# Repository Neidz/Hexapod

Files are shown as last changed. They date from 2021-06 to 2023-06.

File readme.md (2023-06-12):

<b>Update: Well, this code is really bad but if you still want to use it then go ahead, it will work... kinda. No idea what past me was thinking writing it.</b>

<p>This is 3D printed hexapod that I build, it runs on Raspberry Pi, uses 18 servo motors for movement and is controlled from app on the phone. I started this project about year ago and didn't visit it for quite some time but I decided that it's still worth sharing because someone might want find models or code (communication between Raspberry Pi and servo control board was kinda tricky for me) useful.</p>

<h4>Here are some pictures:</h4>
<a>https://imgur.com/a/LP6Iy2R?nc=1</a>

<h4>And here are some videos</h4>
<a>https://www.youtube.com/watch?v=-9L5q-5OcWs</a> </br>
<a>https://www.youtube.com/watch?v=_HX3u8fKZZM</a>

<h4>Main goals of this project were:</h4>
<ul>
<li>building hexapod that is running on Raspberry Pi (there are a lot of them running on arduinos but I wanted to try building one on RPi and that project was my way of learning python)</li>
<li>-creating really affordable robot (most of the things used in my robot are really cheap, even 18 servo motors shouldn't be something out of reach for hobbyist</li>
</ul>

<h1>3D printed parts</h1>

<h4>If you want to print that hexapod you will have to print:</h4>
<ul>
<li>Base in 3 parts (Split_base_1.stl, Split_base_2.stl, Split_base_3.stl) or if you have large 3d printer you can connect parts in any program that allows stl manipulations and print is as one</li>
<li>Cover in 2 parts (Split_cover_1.stl, Split_cover_2.stl), the same things as with base here, if you are able then you can print it as one after connecting it in any program</li>
<li>First_part_of_the_leg.stl x3</li>
<li>First_part_of_the_leg.stl x3 after mirroring</li>
<li>Second_part_of_the_leg.stl x3</li>
<li>Second_part_of_the_leg.stl x3 after mirroring</li>
<li>Third_part_of_the_leg.stl x3</li>
<li>Third_part_of_the_leg.stl x3 after mirroring</li>
  </ul><br>
<p>You have to print all leg parts 3 times and then print them 3 more times after mirroring
I printed all the parts with PLA, 0,1mm layer height worked best for overhangs but you can probably go with 0,2mm, all parts other than cover sadly need some supports</p>

<h1>Software</h1>

<p>I wrote the code in python and it's meant to be run on Raspberry Pi (i used 3b+), I'm uploading this project some time after I actually created it so the way robot is getting all the commands is quite weird but basically: raspberry pi runs 2 programs, one is called Hexapod_server.py and it starts requestHandler which constantly writes all requests it's getting into Requests.txt, after that Hexapod_final.py grabs them from the file and executes functions connected to those requests
<br>
Not the best solution but at the time this was the best things that I came up with while being absolute python noob. To send requests I also created app with Mit app inventorr (not the most elegant thing but once again it was all I could make at the time)</p>

<h4>Setup</h4>
<ul>
<li>in Hexapod_server.py you have to change "Change it to your ip" in line 30 to... well, your ip</li>
<li>in app you have to also pass your ip and click "Set"</li>
</ul>
<h1>Hardware</h1>
<ul>
<li>raspberry pi of your choice (I used 3b+ here)</li>
<li>buck converter that can handle at least 10A at 6,5V for all 18 servos (I used 300W 20A buck converter from aliexpress and it worked fine)</li>
<li>suitable powerbank or next buck converter to power up raspberry pi</li>
<li>MG995 55g servo x18</li>
<li>25T M3 Metal RC Servo Arm Horn x18 (I used this one aliexpress.com/item/4000957433782.html?spm=a2g0s.9042311.0.0.adbd5c0fBZJcos)</li>
<li>at least 18 channel servo control board that is able to handle previously mentioned power (I used this 32 channel board aliexpress.com/item/32272674301.html?spm=a2g0s.9042311.0.0.27425c0f2JeqpC)</li>
<li>battery, preferably 3S, at least 2000mAhm and if you want to also power up raspberry pi from the same battery then I would go for 3000mAh+ (with 2000mAh 3S battery i was able to use hexapod for about 20 minutes while powering raspberry pi from separate powerbank)</li>
<li>cables and connectors of your choice, I wouldn't use jumper wires for main power to servo control board because they are very thin but if you are feeling spicy and like the smell of burning insulation then go ahead </li>
<li>a lot of m3 bolts and preferably m3 locknuts (vibrations cause normal nuts to slowly unscrew)</li>
</ul>

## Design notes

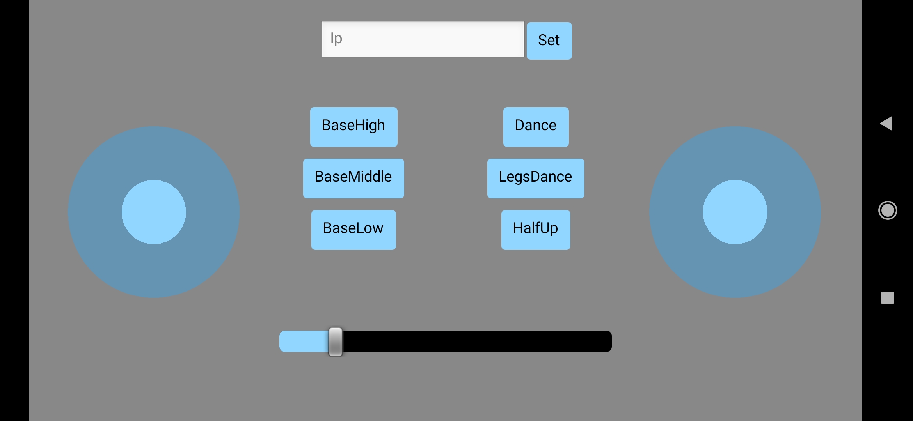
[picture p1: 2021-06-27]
Media/App for hexapod control.jpg

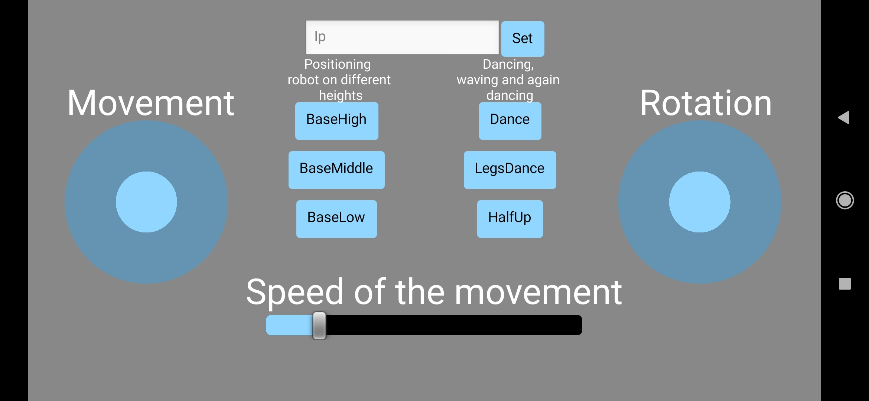
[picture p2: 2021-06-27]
Media/How app works.png

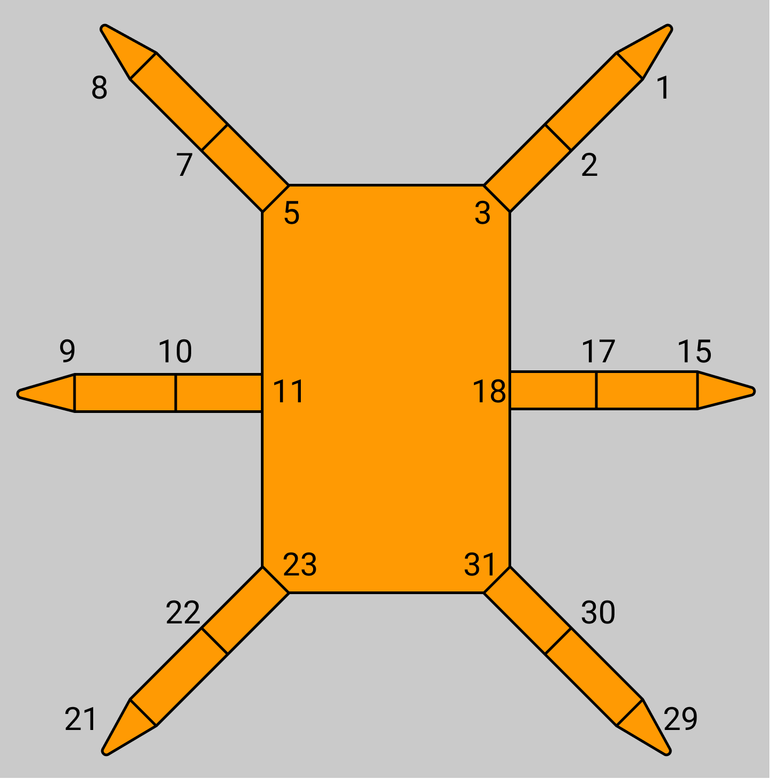
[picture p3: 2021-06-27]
Media/Servo connection.png

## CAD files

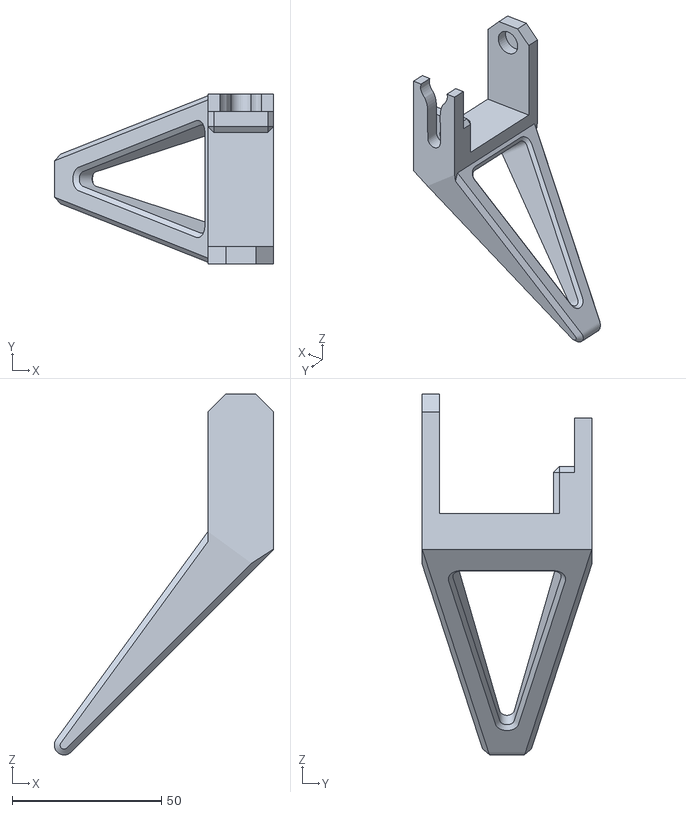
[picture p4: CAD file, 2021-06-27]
Parts stls/Third_part_of_the_leg.stl
73.4 x 57.0 x 120.8

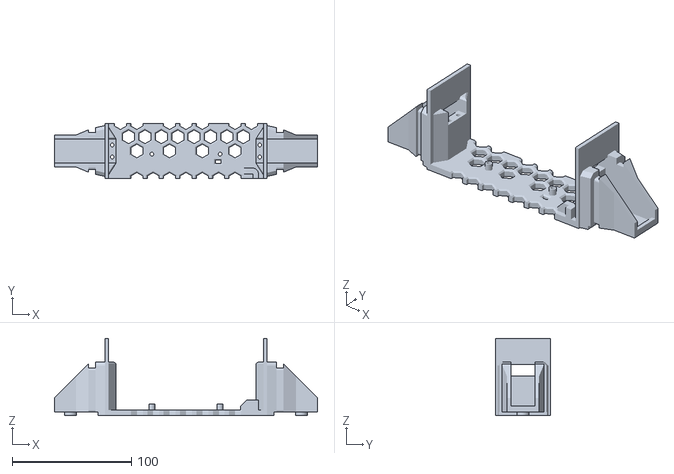
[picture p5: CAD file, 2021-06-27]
Parts stls/Split_base_3.stl
220.8 x 46.0 x 65.0

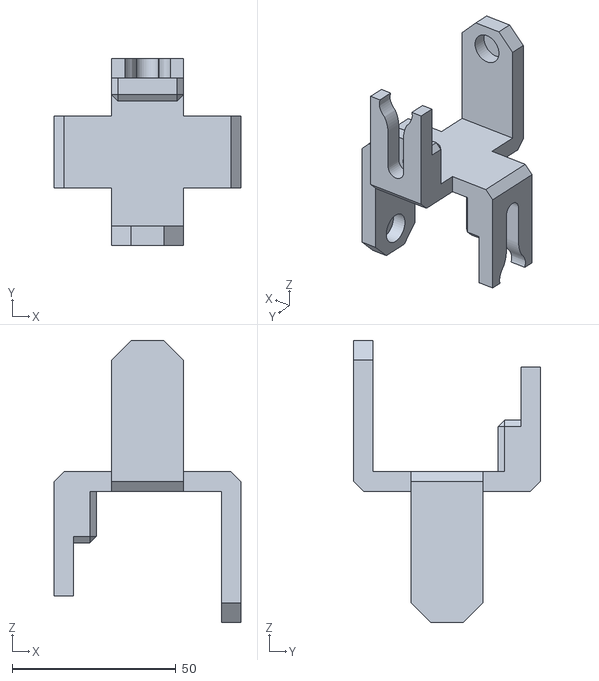
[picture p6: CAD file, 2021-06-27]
Parts stls/First_part_of_the_leg.stl
57.0 x 57.0 x 86.0

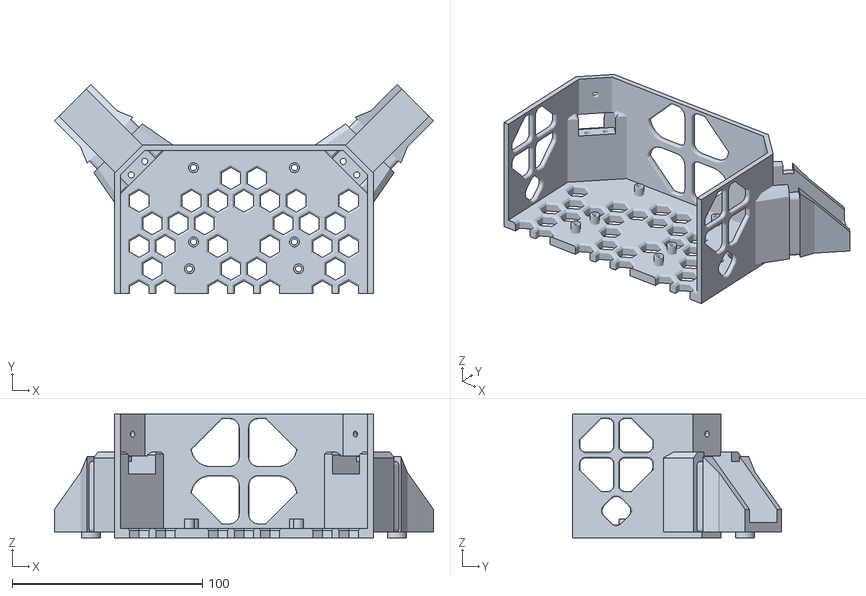
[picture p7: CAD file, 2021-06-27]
Parts stls/Split_base_1.stl
199.0 x 109.6 x 65.0

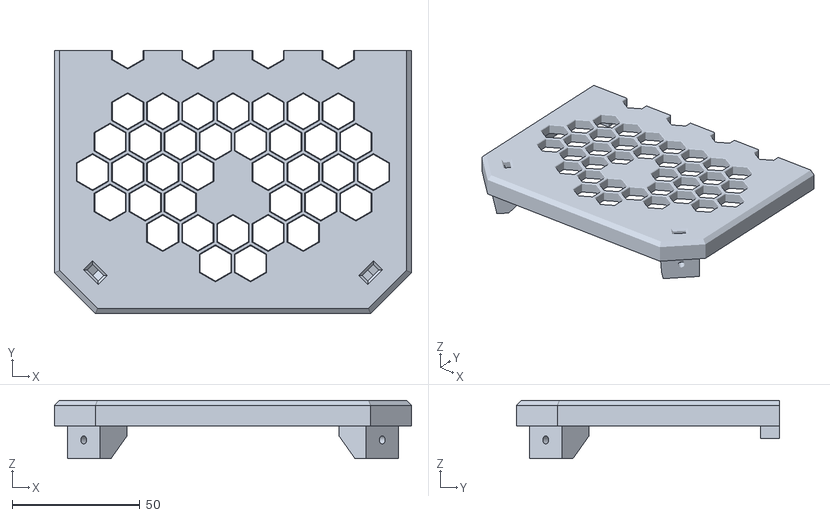
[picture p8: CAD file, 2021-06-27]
Parts stls/Split_cover_2.stl
139.8 x 103.0 x 22.9

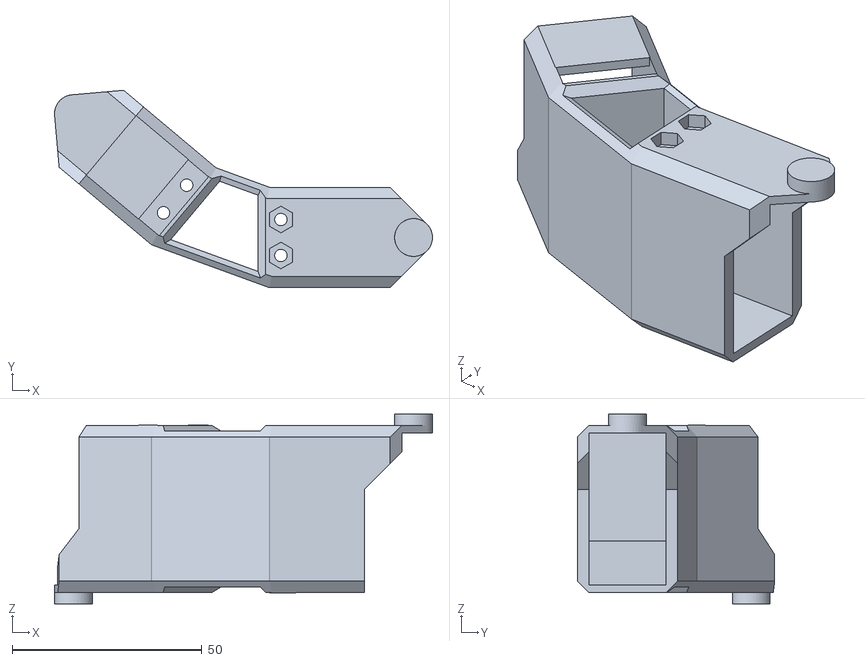
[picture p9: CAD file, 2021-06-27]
Parts stls/Second_part_of_the_leg.stl
99.7 x 52.1 x 50.0

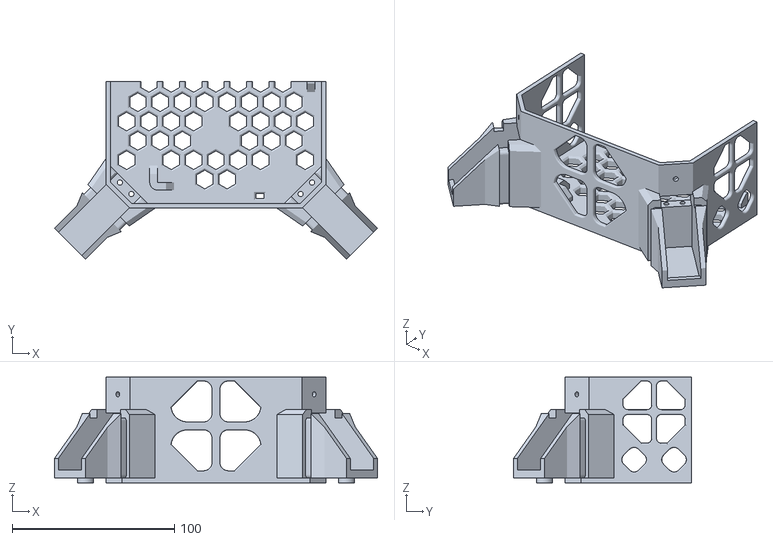
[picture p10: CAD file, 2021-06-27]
Parts stls/Split_base_2.stl
199.0 x 109.6 x 65.0

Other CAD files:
Parts stls/Split_cover_1.stl

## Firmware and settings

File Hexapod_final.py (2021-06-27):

import serial
import time

if __name__ == '__main__':
    ser = serial.Serial('/dev/ttyACM0', baudrate=115200,
                        parity=serial.PARITY_NONE,
                        stopbits=serial.STOPBITS_ONE,
                        bytesize=serial.EIGHTBITS
                        )

fastsleep = 0.5
base = 1500
p2 = p3 = p5 = p6 = p8 = p9 = p11 = p12 = p14 = p15 = p17 = p18 = 1500
p1 = p4 = p7 = 1650
p10 = p16 = p13 = 1350
change = 350
change2 = 170
change3 = change2*2
change4 = 350
change5 = 300
speed = 70
sleep = speed / 1000 + 0.1
slow = 1000
delay = 0
t = 5
hight = "normal"
Request = "base\n"
Request2 = "boop"

def Prepare():
    global base, speed, slow, delay, p1, p2, p3, p4, p5, p6, p7, p8, p9, p10, p11, p12, p13, p14, p15, p16, p17, p18
    base = int(base)
    speed = int(speed)
    slow = int(slow)
    p1, p2, p3, p4, p5, p6, p7, p8, p9, p10, p11, p12, p13, p14, p15, p16, p17, p18 = int(p1), int(p2), int(p3), int(
        p4), int(p5), int(p6), int(p7), int(p8), int(p9), int(p10), int(p11), int(p12), int(p13), int(p14), int(
        p15), int(p16), int(p17), int(p18)


def Reset():
    global base, speed, slow, delay, p1, p2, p3, p4, p5, p6, p7, p8, p9, p10, p11, p12, p13, p14, p15, p16, p17, p18
    base = 1500
    speed = 500
    slow = 1000
    p1 = p2 = p3 = p4 = p5 = p6 = p7 = p8 = p9 = p10 = p11 = p12 = p13 = p14 = p15 = p16 = p17 = p18 = 1500


def BasePosition():
    global base, speed, slow, delay, p1, p2, p3, p4, p5, p6, p7, p8, p9, p10, p11, p12, p13, p14, p15, p16, p17, p18
    if hight == "normal":
        Prepare()
        p2 = p3 = p5 = p6 = p8 = p9 = p11 = p12 = p14 = p15 = p17 = p18 = 1500
        p1 = p4 = p7 = 1650
        p10 = p16 = p13 = 1350
        basep = f"#1P{p10}#2P{p11}#3P{p12}#5P{p3}#7P{p2}#8P{p1}#9P{p4}#10P{p5}#11P{p6}#15P{p13}#17P{p14}#18P{p15}#21P{p7}#22P{p8}#23P{p9}#29P{p16}#30P{p17}#31P{p18}T{speed}D{delay}\r\n".encode()
        ser.write(basep)
    if hight == "low":
        Prepare()
        p3 = p6 = p9 = p12 = p15 = p18 = 1500
        p2 = p5 = p8 = 1200
        p1 = p4 = p7 = 1950
        p11 = p14 = p17 = 1800
        p10 = p16 = p13 = 1050
        basep = f"#1P{p10}#2P{p11}#3P{p12}#5P{p3}#7P{p2}#8P{p1}#9P{p4}#10P{p5}#11P{p6}#15P{p13}#17P{p14}#18P{p15}#21P{p7}#22P{p8}#23P{p9}#29P{p16}#30P{p17}#31P{p18}T{speed}D{delay}\r\n".encode()
        ser.write(basep)
    if hight == "high":
        Prepare()
        p3 = p6 = p9 = p12 = p15 = p18 = 1500
        p2 = p5 = p8 = 1800
        p1 = p4 = p7 = 1350
        p11 = p14 = p17 = 1200
        p10 = p16 = p13 = 1650
        basep = f"#1P{p10}#2P{p11}#3P{p12}#5P{p3}#7P{p2}#8P{p1}#9P{p4}#10P{p5}#11P{p6}#15P{p13}#17P{p14}#18P{p15}#21P{p7}#22P{p8}#23P{p9}#29P{p16}#30P{p17}#31P{p18}T{speed}D{delay}\r\n".encode()
        ser.write(basep)





def Movement():
    movement = f"#1P{p10}#2P{p11}#3P{p12}#5P{p3}#7P{p2}#8P{p1}#9P{p4}#10P{p5}#11P{p6}#15P{p13}#17P{p14}#18P{p15}#21P{p7}#22P{p8}#23P{p9}#29P{p16}#30P{p17}#31P{p18}T{speed}D{delay}\r\n".encode()
    ser.write(movement)


def HalfUp():
    global base, speed, slow, delay, p1, p2, p3, p4, p5, p6, p7, p8, p9, p10, p11, p12, p13, p14, p15, p16, p17, p18
    BasePosition()
def HalfUp2():
    global base, speed, slow, delay, p1, p2, p3, p4, p5, p6, p7, p8, p9, p10, p11, p12, p13, p14, p15, p16, p17, p18
    time.sleep(sleep)
    Prepare()
    p1, p2, p7, p8 = p1 + change, p2 - change, p7 + change, p8 - change
    p13, p14 = p13 - change, p14 + change
    Movement()
    time.sleep(sleep)
    BasePosition()
    time.sleep(sleep)
    Prepare()
    p4, p5 = p4 + change, p5 - change
    p10, p11, p16, p17 = p10 - change, p11 + change, p16 - change, p17 + change
    Movement()
    time.sleep(sleep)
    BasePosition()
    LineCheck()

def Dance():
    global base, speed, slow, delay, p1, p2, p3, p4, p5, p6, p7, p8, p9, p10, p11, p12, p13, p14, p15, p16, p17, p18
    BasePosition()
def Dance2():
    global base, speed, slow, delay, p1, p2, p3, p4, p5, p6, p7, p8, p9, p10, p11, p12, p13, p14, p15, p16, p17, p18
    time.sleep(sleep)
    Prepare()
    p1, p2, p3, p16, p17, p18 = p1 + change, p2 - change, p3 + change4, p16 - change, p17 + change, p18 + change4
    Movement()
    time.sleep(sleep)
    Prepare()
    p1, p2, p16, p17 = p1 - change, p2 + change, p16 + change, p17 - change
    Movement()
    time.sleep(sleep)
    Prepare()
    p1, p2, p3, p16, p17, p18 = p1 + change, p2 - change, p3 - change4, p16 - change, p17 + change, p18 - change4
    Movement()
    time.sleep(sleep)
    Prepare()
    p1, p2, p16, p17 = p1 - change, p2 + change, p16 + change, p17 - change
    Movement()
    time.sleep(sleep)
    Prepare()
    p10, p11, p12, p7, p8, p9 = p10 - change, p11 + change, p12 - change4, p7 + change, p8 - change, p9 - change4
    Movement()
    time.sleep(sleep)
    Prepare()
    p10, p11, p7, p8, = p10 + change, p11 - change, p7 - change, p8 + change
    Movement()
    time.sleep(sleep)
    Prepare()
    p10, p11, p12, p7, p8, p9 = p10 - change, p11 + change, p12 + change4, p7 + change, p8 - change, p9 + change4
    Movement()
    time.sleep(sleep)
    Prepare()
    p10, p11, p7, p8, = p10 + change, p11 - change, p7 - change, p8 + change
    Movement()
    time.sleep(sleep)
    Prepare()
    LineCheck()


def Forward():
    global base, speed, slow, delay, p1, p2, p3, p4, p5, p6, p7, p8, p9, p10, p11, p12, p13, p14, p15, p16, p17, p18
    BasePosition()
    time.sleep(sleep)
    Prepare()
    p7, p8, p9 = p7 + change, p8 - change, p9 - change4
    Movement()
    time.sleep(sleep)
    Prepare()
    p7, p8 = p7 - change, p8 + change
    Movement()
    time.sleep(sleep)
    Prepare()
    p16, p17, p18 = p16 - change, p17 + change, p18 + change4
    Movement()
    time.sleep(sleep)
    Prepare()
    p16, p17 = p16 + change, p17 - change
    Movement()
    time.sleep(sleep)
    Prepare()
    p1, p2, p7, p8, p13, p14, p15 = p1 + change, p2 - change, p7 + change, p8 - change, p13 - change, p14 + change, p15 + change2
    p6, p12, p18 = p6 + change2, p12 - change4, p18 - change4
    Movement()
    time.sleep(sleep)
def Forward2():
    global base, speed, slow, delay, p1, p2, p3, p4, p5, p6, p7, p8, p9, p10, p11, p12, p13, p14, p15, p16, p17, p18
    Prepare()
    p1, p2, p7, p8, p13, p14 = p1 - change, p2 + change, p7 - change, p8 + change, p13 + change, p14 - change
    Movement()
    time.sleep(sleep)
    Prepare()
    p3, p9, p15 = p3 + change4, p9 + change4, p15 - change3
    p6, p12, p18 = p6 - change3, p12 + change4, p18 + change4
    p4, p5, p10, p11, p16, p17 = p4 + change, p5 - change, p10 - change, p11 + change, p16 - change, p17 + change
    Movement()
    time.sleep(sleep)
    Prepare()
    p4, p5, p10, p11, p16, p17 = p4 - change, p5 + change, p10 + change, p11 - change, p16 + change, p17 - change
    Movement()
    time.sleep(sleep)
    Prepare()
    p6, p12, p18 = p6 + change3, p12 - change4, p18 - change4
    p3, p9, p15 = p3 - change4, p9 - change4, p15 + change3
    p1, p2, p7, p8, p13, p14 = p1 + change, p2 - change, p7 + change, p8 - change, p13 - change, p14 + change
    Movement()
    time.sleep(sleep)
    LineCheck()

def Back():
    global base, speed, slow, delay, p1, p2, p3, p4, p5, p6, p7, p8, p9, p10, p11, p12, p13, p14, p15, p16, p17, p18
    BasePosition()
    time.sleep(sleep)
    Prepare()
    p1, p2, p3 = p1 + change, p2 - change, p3 + change4
    Movement()
    time.sleep(sleep)
    Prepare()
    p1, p2 = p1 - change, p2 + change
    Movement()
    time.sleep(sleep)
    Prepare()
    p10, p11, p12 = p10 - change, p11 + change, p12 - change4
    Movement()
    time.sleep(sleep)
    Prepare()
    p10, p11 = p10 + change, p11 - change
    Movement()
    time.sleep(sleep)
    Prepare()
    p1, p2, p7, p8, p13, p14, p15 = p1 + change, p2 - change, p7 + change, p8 - change, p13 - change, p14 + change, p15 - change2
    p6, p12, p18 = p6 - change2, p12 + change4, p18 + change4
    Movement()
    time.sleep(sleep)
def Back2():
    global base, speed, slow, delay, p1, p2, p3, p4, p5, p6, p7, p8, p9, p10, p11, p12, p13, p14, p15, p16, p17, p18
    Prepare()
    p1, p2, p7, p8, p13, p14 = p1 - change, p2 + change, p7 - change, p8 + change, p13 + change, p14 - change
    Movement()
    time.sleep(sleep)
    Prepare()
    p3, p9, p15 = p3 - change4, p9 - change4, p15 + change3
    p6, p12, p18 = p6 + change3, p12 - change4, p18 - change4
    p4, p5, p10, p11, p16, p17 = p4 + change, p5 - change, p10 - change, p11 + change, p16 - change, p17 + change
    Movement()
    time.sleep(sleep)
    Prepare()
    p4, p5, p10, p11, p16, p17 = p4 - change, p5 + change, p10 + change, p11 - change, p16 + change, p17 - change
    Movement()
    time.sleep(sleep)
    Prepare()
    p6, p12, p18 = p6 - change3, p12 + change4, p18 + change4
    p3, p9, p15 = p3 + change4, p9 + change4, p15 - change3
    p1, p2, p7, p8, p13, p14 = p1 + change, p2 - change, p7 + change, p8 - change, p13 - change, p14 + change
    Movement()
    time.sleep(sleep)
    LineCheck()

def TurnLeft():
    global base, speed, slow, delay, p1, p2, p3, p4, p5, p6, p7, p8, p9, p10, p11, p12, p13, p14, p15, p16, p17, p18
    BasePosition()
    time.sleep(sleep)
    Prepare()
    p1, p2, p7, p8, p13, p14 = p1 + change, p2 - change, p7 + change, p8 - change, p13 - change, p14 + change
    p3, p15 = p3 + change4, p15 + change2
    Movement()
    time.sleep(sleep)
    Prepare()
    p1, p2, p7, p8, p13, p14 = p1 - change, p2 + change, p7 - change, p8 + change, p13 + change, p14 - change
    Movement()
    time.sleep(sleep)
    Prepare()
    p3, p9, p15 = p3 - change4, p9 - change4, p15 - change3
    p4, p5, p10, p11, p16, p17 = p4 + change, p5 - change, p10 - change, p11 + change, p16 - change, p17 + change
    p6, p18 = p6 + change2, p18 + change4
    Movement()
    time.sleep(sleep)
def TurnLeft2():
    global base, speed, slow, delay, p1, p2, p3, p4, p5, p6, p7, p8, p9, p10, p11, p12, p13, p14, p15, p16, p17, p18
    Prepare()
    p4, p5, p10, p11, p16, p17 = p4 - change, p5 + change, p10 + change, p11 - change, p16 + change, p17 - change
    Movement()
    time.sleep(sleep)
    Prepare()
    p3, p9, p15 = p3 + change4, p9 + change4, p15 + change4
    p6, p12, p18 = p6 - change4, p12 - change4, p18 - change4
    p1, p2, p7, p8, p13, p14 = p1 + change, p2 - change, p7 + change, p8 - change, p13 - change, p14 + change
    Movement()
    time.sleep(sleep)
    Prepare()
    p1, p2, p7, p8, p13, p14 = p1 - change, p2 + change, p7 - change, p8 + change, p13 + change, p14 - change
    Movement()
    time.sleep(sleep)
    Prepare()
    p3, p9, p15 = p3 - change4, p9 - change4, p15 - change4
    p6, p12, p18 = p6 + change3, p12 + change4, p18 + change4
    p4, p5, p10, p11, p16, p17 = p4 + change, p5 - change, p10 - change, p11 + change, p16 - change, p17 + change
    Movement()
    time.sleep(sleep)
    LineCheck()


def TurnRight():
    global base, speed, slow, delay, p1, p2, p3, p4, p5, p6, p7, p8, p9, p10, p11, p12, p13, p14, p15, p16, p17, p18
    BasePosition()
    time.sleep(sleep)
    Prepare()
    p10, p11, p16, p17, p4, p5 = p10 - change, p11 + change, p16 - change, p17 + change, p4 + change, p5 - change
    p12, p6 = p12 - change4, p6 - change2
    Movement()
    time.sleep(sleep)
    Prepare()
    p10, p11, p16, p17, p4, p5 = p10 + change, p11 - change, p16 + change, p17 - change, p4 - change, p5 + change
    Movement()
    time.sleep(sleep)
    Prepare()
    p12, p18, p6 = p12 + change4, p18 + change4, p6 + change3
    p13, p14, p1, p2, p7, p8 = p13 - change, p14 + change, p1 + change, p2 - change, p7 + change, p8 - change
    p15, p9 = p15 - change2, p9 - change4
    Movement()
    time.sleep(sleep)
def TurnRight2():
    global base, speed, slow, delay, p1, p2, p3, p4, p5, p6, p7, p8, p9, p10, p11, p12, p13, p14, p15, p16, p17, p18
    Prepare()
    p13, p14, p1, p2, p7, p8 = p13 + change, p14 - change, p1 - change, p2 + change, p7 - change, p8 + change
    Movement()
    time.sleep(sleep)
    Prepare()
    p12, p18, p6 = p12 - change4, p18 - change4, p6 - change4
    p15, p3, p9 = p15 + change4, p3 + change4, p9 + change4
    p10, p11, p16, p17, p4, p5 = p10 - change, p11 + change, p16 - change, p17 + change, p4 + change, p5 - change
    Movement()
    time.sleep(sleep)
    Prepare()
    p10, p11, p16, p17, p4, p5 = p10 + change, p11 - change, p16 + change, p17 - change, p4 - change, p5 + change
    Movement()
    time.sleep(sleep)
    Prepare()
    p12, p18, p6 = p12 + change4, p18 + change4, p6 + change4
    p15, p3, p9 = p15 - change3, p3 - change4, p9 - change4
    p13, p14, p1, p2, p7, p8 = p13 - change, p14 + change, p1 + change, p2 - change, p7 + change, p8 - change
    Movement()
    time.sleep(sleep)
    LineCheck()

def FrontLegsDance():
    global base, speed, slow, delay, p1, p2, p3, p4, p5, p6, p7, p8, p9, p10, p11, p12, p13, p14, p15, p16, p17, p18
    BasePosition()
    time.sleep(sleep)
    Prepare()
    p4, p5, p6, p13, p14, p15 = p4 + change, p5 - change, p6 - change2, p13 - change, p14 + change, p15 + change2
    Movement()
    time.sleep(sleep)
    Prepare()
    p4, p5, p13, p14 = p4 - change, p5 + change, p13 + change, p14 - change
    Movement()
    time.sleep(sleep)
    Prepare()
    p8, p7, p17, p16 = p8 - change5, p7 + change5, p17 + change5, p16 - change5
    Movement()
    time.sleep(sleep)
    Prepare()
    p1, p2, p3, p10, p11, p12 = p1 - change*2.5, p2 - change*2.5, p3 - change4, p10 + change*2, p11 + change*2, p12 - change4
    Movement()
    time.sleep(sleep)
def FrontLegsDance2():
    global base, speed, slow, delay, p1, p2, p3, p4, p5, p6, p7, p8, p9, p10, p11, p12, p13, p14, p15, p16, p17, p18
    Prepare()
    p3, p12 = p3 + change4*1.5, p12 + change4*1.5
    Movement()
    time.sleep(sleep*3)
    Prepare()
    p3, p12 = p3 - change4*1.5, p12 - change4*1.5
    Movement()
    time.sleep(sleep*3)
    LineCheck()

def GoLeft():
    global base, speed, slow, delay, p1, p2, p3, p4, p5, p6, p7, p8, p9, p10, p11, p12, p13, p14, p15, p16, p17, p18
    BasePosition()
    time.sleep(sleep)
    Prepare()
    p13, p14 = p13 - change, p14 + change
    Movement()
    time.sleep(sleep)
    Prepare()
    p14 = p14 - change
    Movement()
    time.sleep(sleep)
    Prepare()
    p3, p9, p13 = p3 - change4, p9 + change4, p13 + change
    p4, p5, p10, p11, p12, p16, p17, p18 = p4 + change, p5 - change, p10 - change, p11 + change, p12 + change4, p16 - change, p17 + change, p18 - change4
    Movement()
    time.sleep(sleep)
    Prepare()
    p4, p5, p10, p11, p16, p17 = p4 - change, p5 + change, p10 + change, p11 - change, p16 + change, p17 - change
    Movement()
    time.sleep(sleep)
def GoLeft2():
    global base, speed, slow, delay, p1, p2, p3, p4, p5, p6, p7, p8, p9, p10, p11, p12, p13, p14, p15, p16, p17, p18
    Prepare()
    p4, p12, p18 = p4 + change, p12 - change4, p18 + change4
    p1, p2, p3, p7, p8, p9, p13, p14 = p1 + change, p2 - change, p3 + change4, p7 + change, p8 - change, p9 - change4, p13 - change, p14 + change
    Movement()
    time.sleep(sleep)
    Prepare()
    p1, p2, p7, p8, p14 = p1 - change, p2 + change, p7 - change, p8 + change, p14 - change
    Movement()
    time.sleep(sleep)
    Prepare()
    p3, p9, p13 = p3 - change4, p9 + change4, p13 + change
    p4, p5, p10, p11, p12, p16, p17, p18 = p4 - change, p5 - change, p10 - change, p11 + change, p12 + change4, p16 - change, p17 + change, p18 - change4
    Movement()
    time.sleep(sleep)
    Prepare()
    p5, p10, p11, p16, p17 = p5 + change, p10 + change, p11 - change, p16 + change, p17 - change
    Movement()
    time.sleep(sleep)
    LineCheck()

def GoRight():
    global base, speed, slow, delay, p1, p2, p3, p4, p5, p6, p7, p8, p9, p10, p11, p12, p13, p14, p15, p16, p17, p18
    BasePosition()
    time.sleep(sleep)
    Prepare()
    p4, p5 = p4 + change, p5 - change
    Movement()
    time.sleep(sleep)
    Prepare()
    p5 = p5 + change
    Movement()
    time.sleep(sleep)
    Prepare()
    p12, p18, p4 = p12 + change4, p18 - change4, p4 - change
    p13, p14, p1, p2, p3, p7, p8, p9 = p13 - change, p14 + change, p1 + change, p2 - change, p3 - change4, p7 + change, p8 - change, p9 + change4
    Movement()
    time.sleep(sleep)
    Prepare()
    p13, p14, p1, p2, p7, p8 = p13 + change, p14 - change, p1 - change, p2 + change, p7 - change, p8 + change
    Movement()
    time.sleep(sleep)
def GoRight2():
    global base, speed, slow, delay, p1, p2, p3, p4, p5, p6, p7, p8, p9, p10, p11, p12, p13, p14, p15, p16, p17, p18
    Prepare()
    p13, p3, p9 = p13 - change, p3 + change4, p9 - change4
    p10, p11, p12, p16, p17, p18, p4, p5 = p10 - change, p11 + change, p12 - change4, p16 - change, p17 + change, p18 + change4, p4 + change, p5 - change
    Movement()
    time.sleep(sleep)
    Prepare()
    p10, p11, p16, p17, p5 = p10 + change, p11 - change, p16 + change, p17 - change, p5 + change
    Movement()
    time.sleep(sleep)
    Prepare()
    p12, p18, p4 = p12 + change4, p18 - change4, p4 - change
    p13, p14, p1, p2, p3, p7, p8, p9 = p13 + change, p14 + change, p1 + change, p2 - change, p3 - change4, p7 + change, p8 - change, p9 + change4
    Movement()
    time.sleep(sleep)
    Prepare()
    p14, p1, p2, p7, p8 = p14 - change, p1 - change, p2 + change, p7 - change, p8 + change
    Movement()
    time.sleep(sleep)
    LineCheck()




def LineCheck():
    global line, Request
    with open("Request.txt", "r") as file:
        for line in file:
            pass
        Request = line.strip("\n")
        print(line)
        file.close()

line = "boop"
while True:
    LineCheck()
    if Request == Request2:
        print("all good")
        time.sleep(0.1)
    elif Request is not Request2:
        Request2 = Request
        Request3 = Request2
        if Request3 == 'forward':
            Forward()
            LineCheck()
            while Request == 'forward':
                Forward2()
        elif Request3 == 'back':
            print(Request3)
            Back()
            LineCheck()
            while Request == 'back':
                Back2()
        elif Request3 == 'turnleft':
            print(Request3)
            TurnLeft()
            LineCheck()
            while Request == 'turnleft':
                TurnLeft2()
        elif Request3 == 'turnright':
            TurnRight()
            LineCheck()
            while Request == 'turnright':
                TurnRight2()
        elif Request3 == 'base':
            BasePosition()
        elif Request3 == 'dance':
            Dance()
            LineCheck()
            while Request == 'dance':
                Dance2()
        elif Request3 == 'halfup':
            HalfUp()
            LineCheck()
            while Request == 'halfup':
                HalfUp2()
        elif Request3 == 'frontlegsdance':
            print(Request3)
            FrontLegsDance()
            LineCheck()
            while Request == 'frontlegsdance':
                FrontLegsDance2()
        elif Request3 == 'goleft':
            print(Request3)
            GoLeft()
            LineCheck()
            while Request == 'goleft':
                GoLeft2()
        elif Request3 == 'goright':
            print(Request3)
            GoRight()
            LineCheck()
            while Request == 'goright':
                GoRight2()
        elif Request3 == 'basehigh':
            hight = "high"
        elif Request3 == 'basemiddle':
            hight = "normal"
        elif Request3 == 'baselow':
            hight = "low"
        else:
            Request3 = Request
            Request3 = float(Request3)
            if Request3 < 10000:
                s = Request3
                s = float(s)
                speed = s
                sleep = speed / 1000 + 0.1
            else:
                print("wut")
    else:
        print("No idea why")
    time.sleep(0.1)

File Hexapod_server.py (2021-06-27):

import time
from http.server import BaseHTTPRequestHandler, HTTPServer

Req = open("Request.txt", "w")
Req.close()
Request2 = "foo"
class RequestHandler_httpd(BaseHTTPRequestHandler):
  def do_GET(self):
    global Request, Request2
    messagetosend = bytes('Change it to name',"utf")
    self.send_response(200)
    self.send_header('Content-Type', 'text/plain')
    self.send_header('Content-Length', len(messagetosend))
    self.end_headers()
    self.wfile.write(messagetosend)
    Request = self.requestline
    Request = Request[5 : int(len(Request)-9)]
    print(Request)
    global hight, speed, sleep
    if Request == Request2:
        print("all good")
    elif Request is not Request2:
        Request2 = Request
        Req = open("Request.txt", "a")
        Req.write(Request + "\n")
        Req.close()
    return


server_address_httpd = ('Change it to your ip',8080)
httpd = HTTPServer(server_address_httpd, RequestHandler_httpd)
print('Starting server:')
httpd.serve_forever()
